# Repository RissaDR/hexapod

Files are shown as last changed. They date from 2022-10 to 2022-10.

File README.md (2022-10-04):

# hexapod

This is a hexapod robot project, designed to be built with 18 HerkuleX DRS-0101 servos. The frame of the hexapod robot was initially intended to be build with acrylic (plexiglass) sheets and hand-cut, but after some attempts at cutting the acrylic, it was decided it would be more efficient and accurate to 3D print the frame instead.

The constructed hexapod with the servos and 3D printed parts:

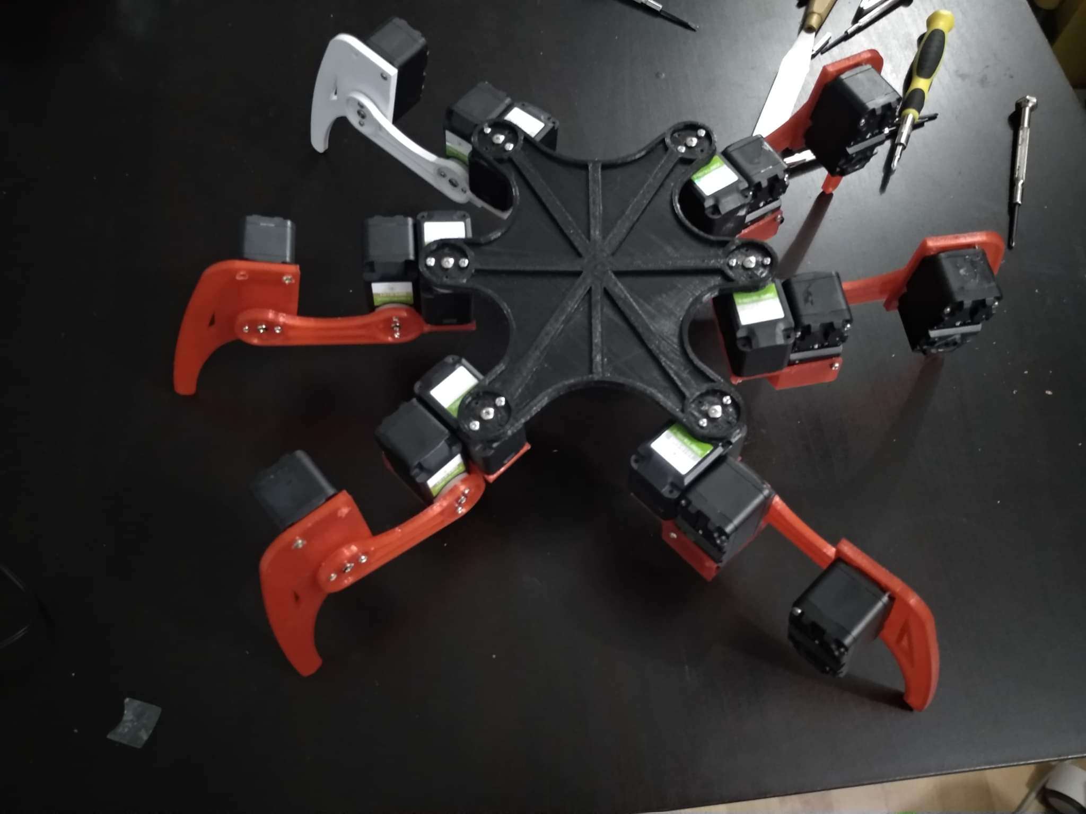
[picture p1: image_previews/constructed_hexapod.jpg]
Constructed hexapod


## Simulation of kinematics

With help from a [hexapod robot simulator](https://github.com/mithi/hexapod) the inverse kinematics of the robot and its corresponding servo movements were solved by scripting a gait simulator with a skeleton hexapod model made in Blender using Python.

Simulating kinematics with a Python script to animate skeleton hexapod model in Blender:

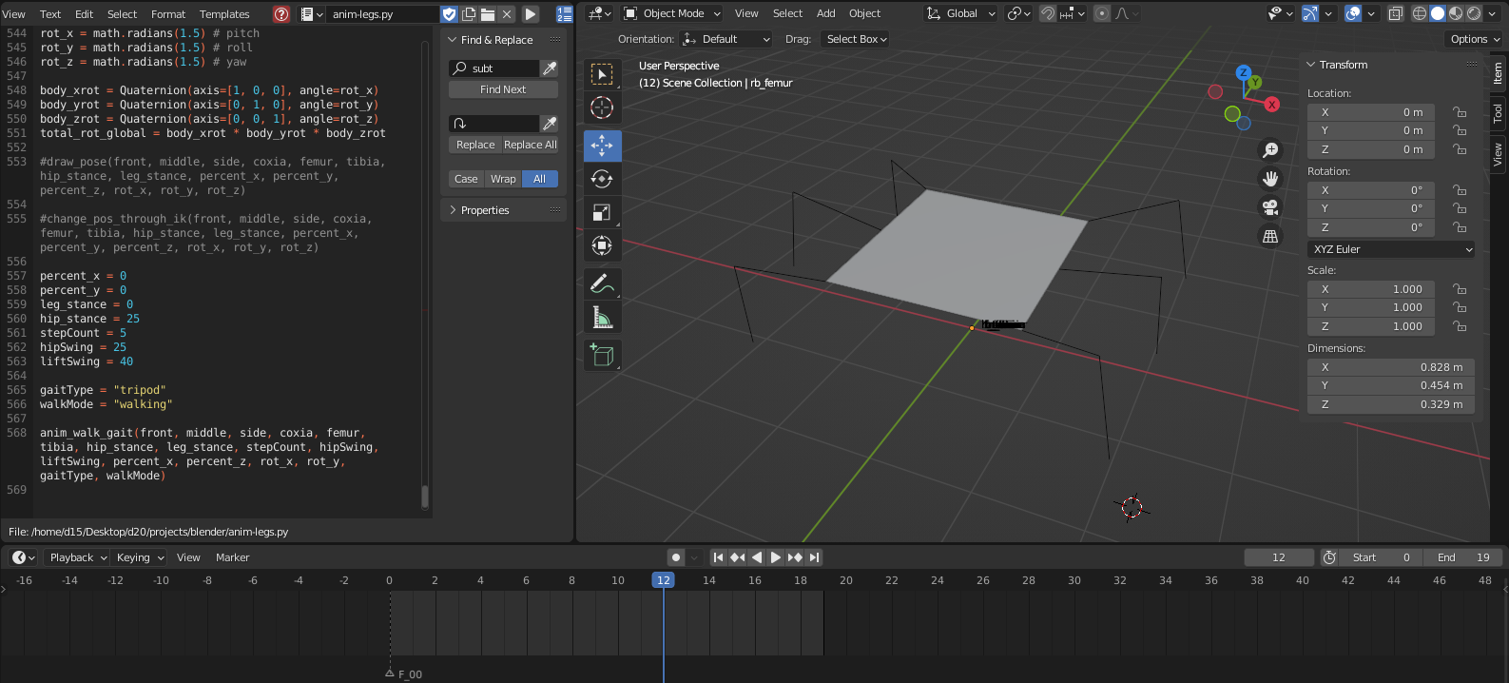
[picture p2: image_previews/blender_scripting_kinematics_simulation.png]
Simulating kinematics with a Python script on a skeleton hexapod model in Blender


## Creation of the hexapod frame

The hexapod frame was modelled with mainly the measurements and the dimensions, as well as movement range of the HerkuleX DRS-0101 servos in mind. Before switching over to 3D printed this model was used to create the acrylic blueprints to cut out the hexapod frame. The frame was modelled to size using Blender in `model/blender/my_hexapod_frame.blend` and exported to .stl and then used Cura to generate its .gcode to print with a 3D printer using Pronterface. 

Through several printing trials the scale of some of the parts of the frame were slightly adjusted and the .stl and .gcode of iterations of these trials are in the repository in `model/blender/stl/` and `model/blender/gcode/` respectively.

3D model of hexapod in Blender, with parts positioned as they would be constructed:

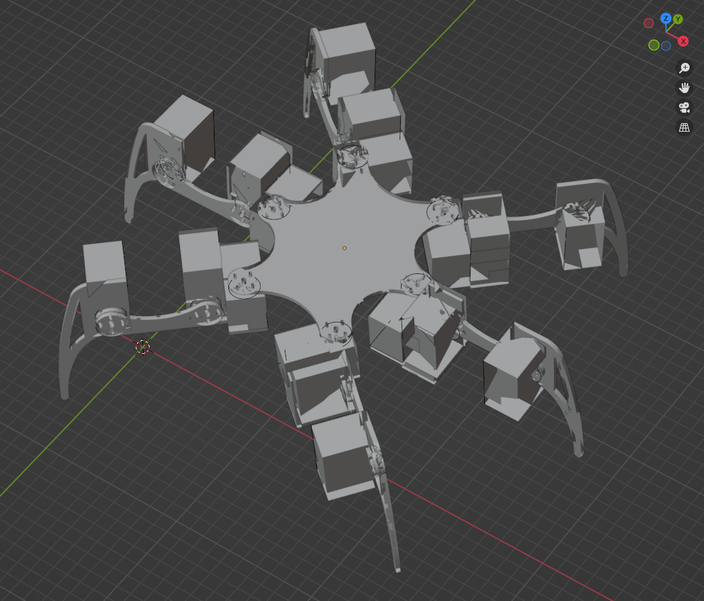
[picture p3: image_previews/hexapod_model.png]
3D model of hexapod in Blender


Wireframe of 3D model:

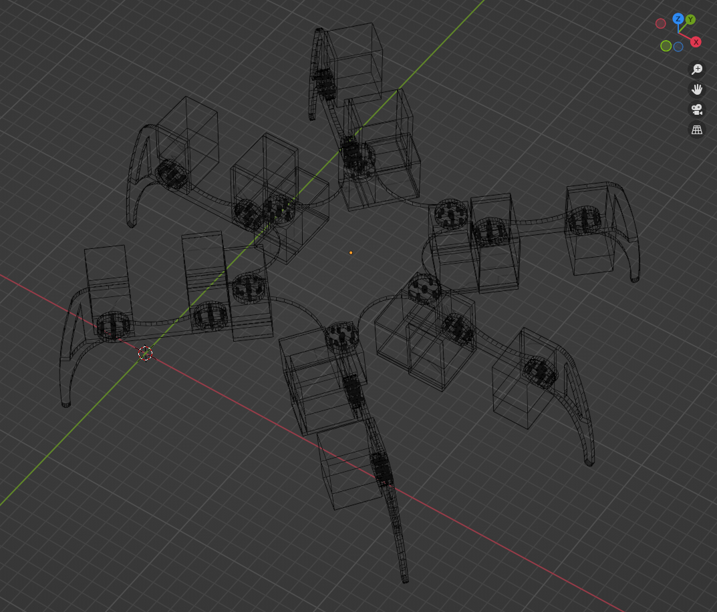
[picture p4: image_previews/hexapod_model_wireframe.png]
3D model of hexapod in Blender, wireframe view


Overview of parts on acrylic blueprint from `model/acrylic_blueprints/`:

Overview of parts on acrylic blueprint

## Interfacing with the servos

To interface with and move the servos an Arduino microcontroller was used; with an ESP32 microcontroller the servos on the hexapod could also be controlled using Wi-Fi/Bluetooth. To test for driver issues on the motor this project also wrote some test scripts in Python.

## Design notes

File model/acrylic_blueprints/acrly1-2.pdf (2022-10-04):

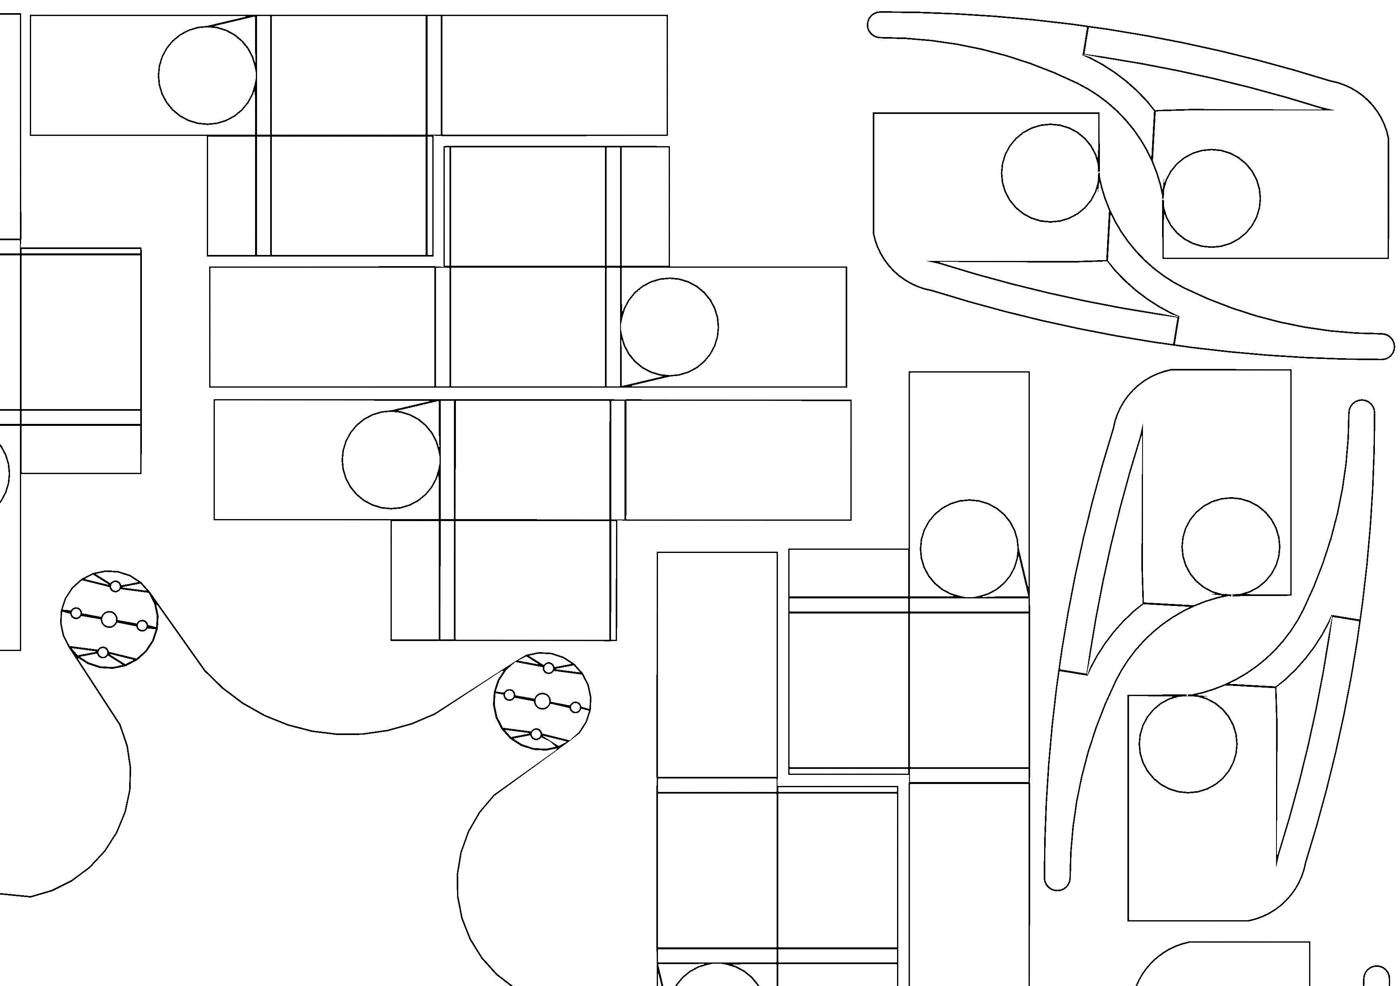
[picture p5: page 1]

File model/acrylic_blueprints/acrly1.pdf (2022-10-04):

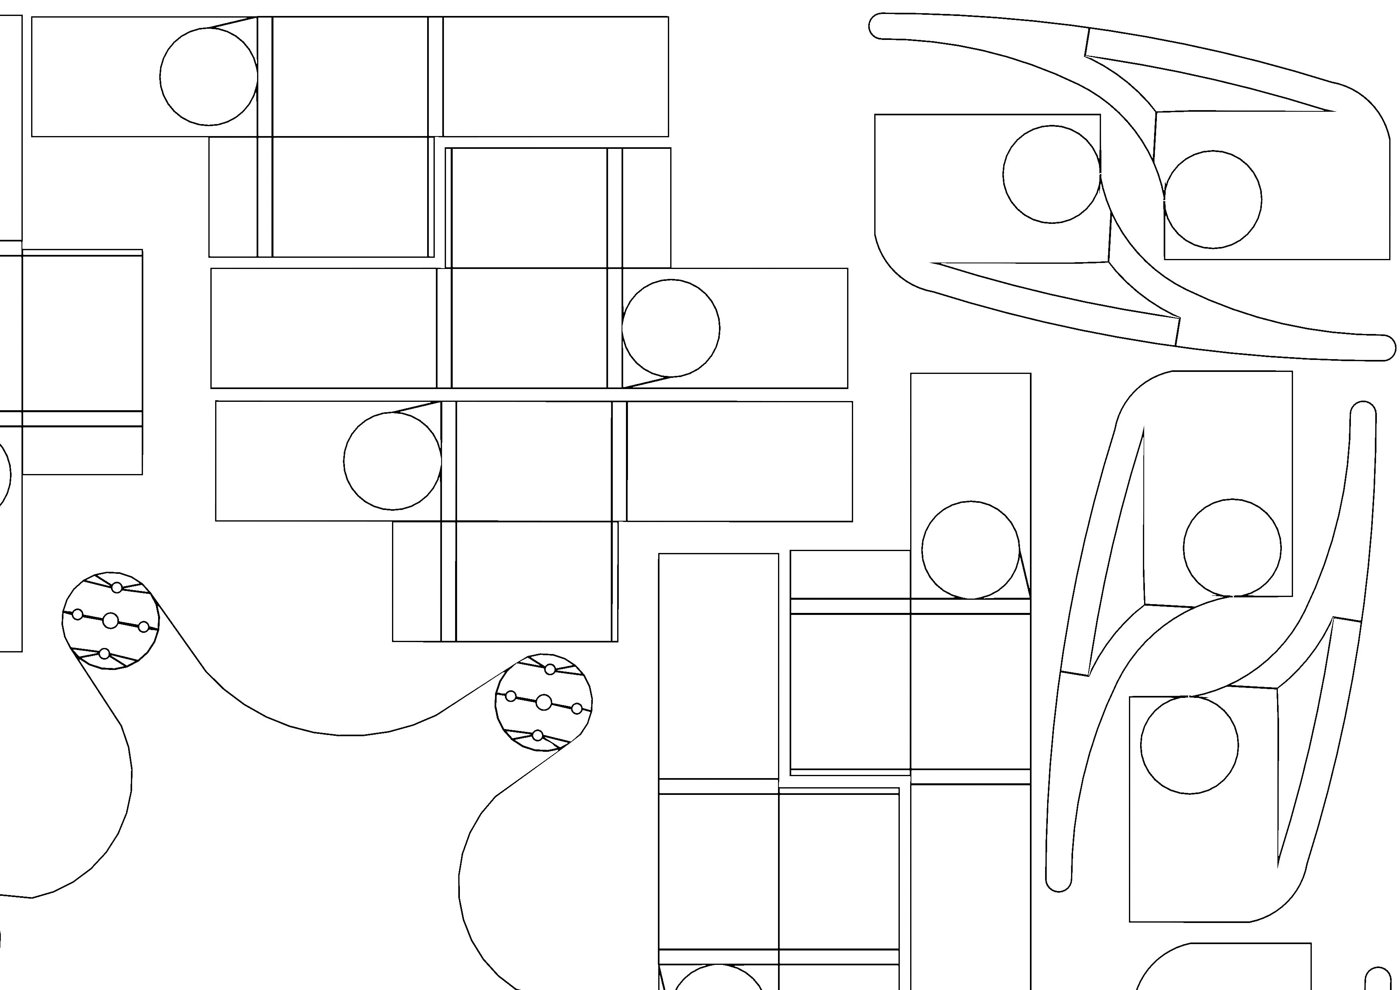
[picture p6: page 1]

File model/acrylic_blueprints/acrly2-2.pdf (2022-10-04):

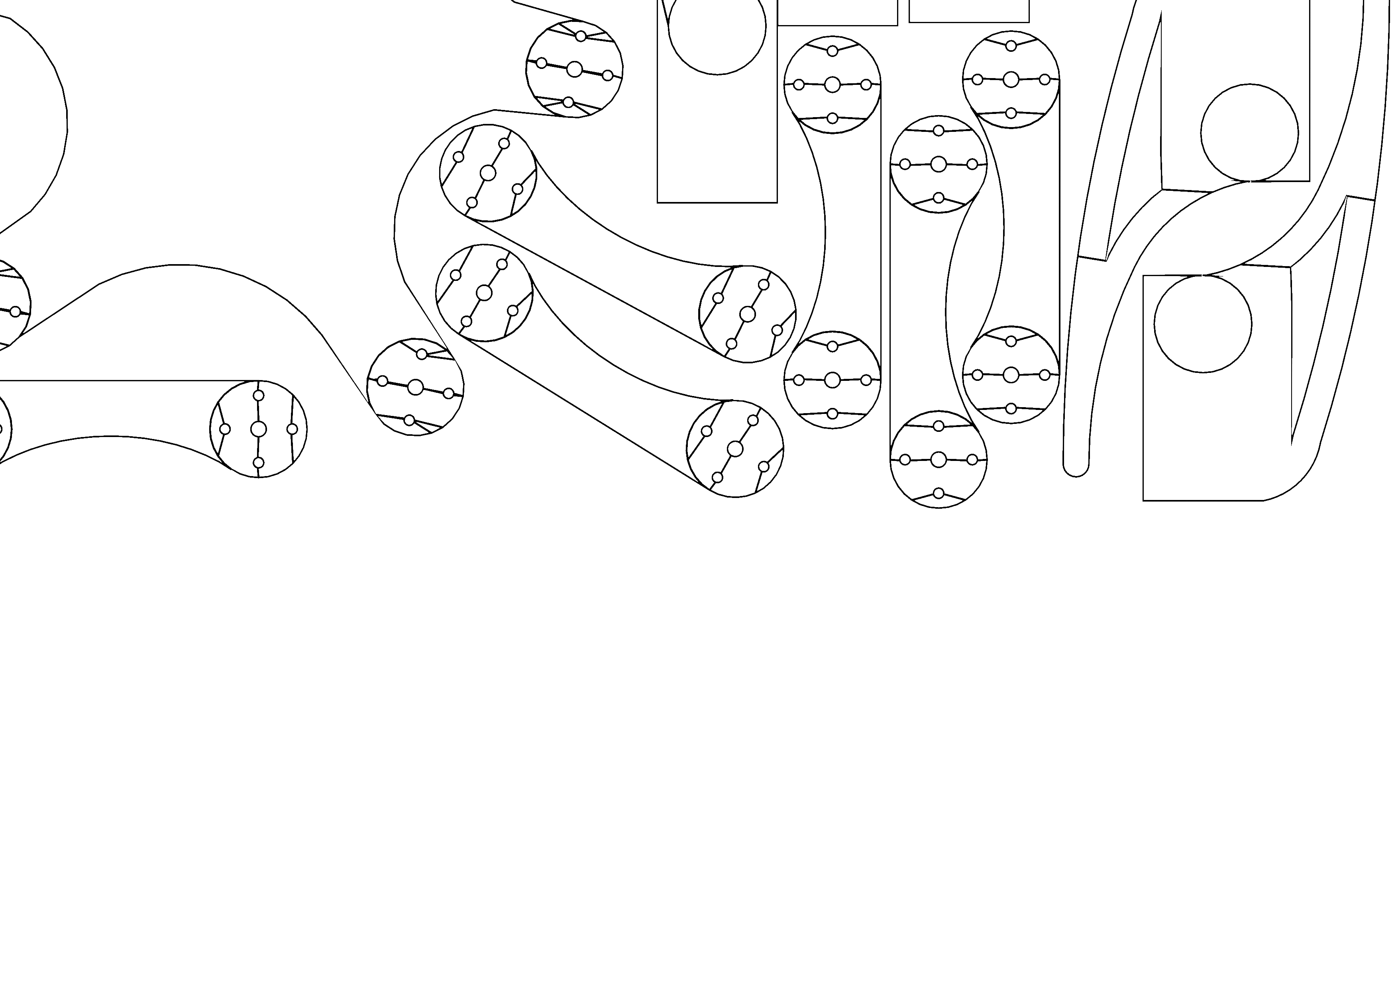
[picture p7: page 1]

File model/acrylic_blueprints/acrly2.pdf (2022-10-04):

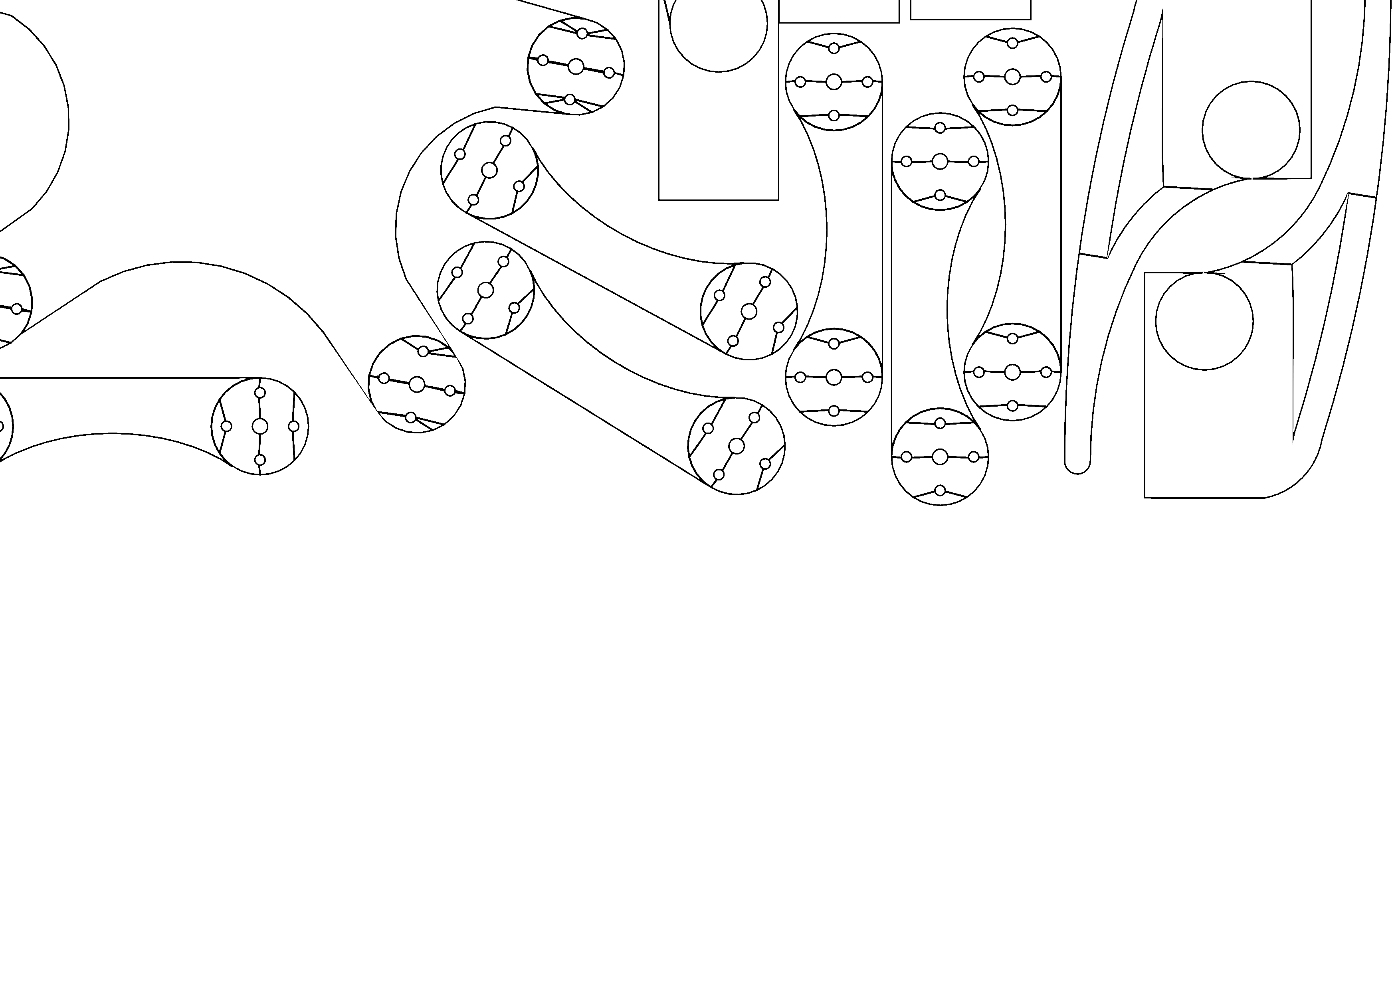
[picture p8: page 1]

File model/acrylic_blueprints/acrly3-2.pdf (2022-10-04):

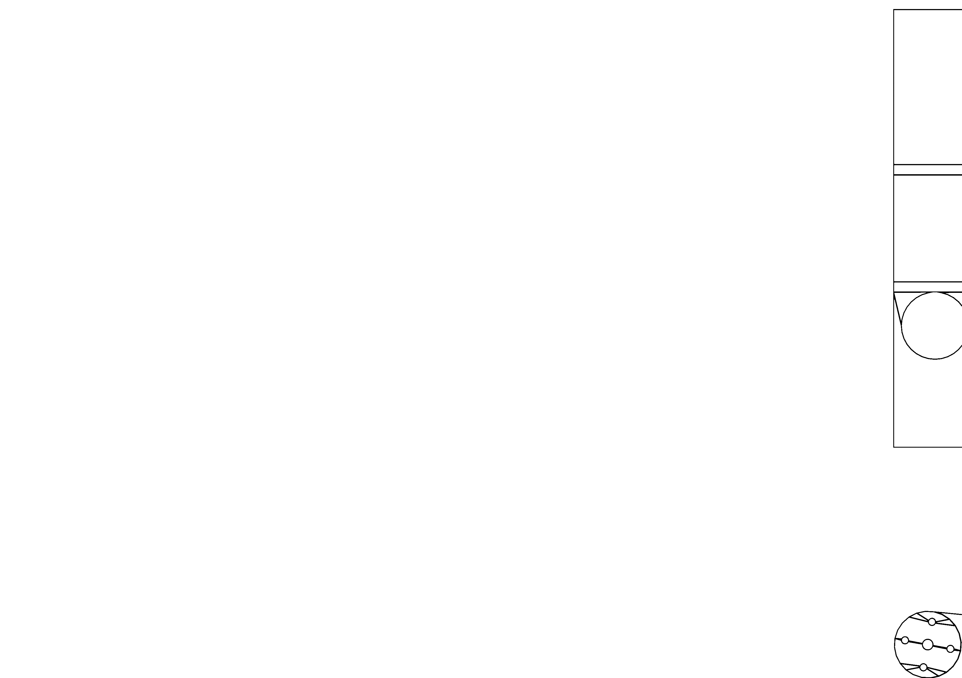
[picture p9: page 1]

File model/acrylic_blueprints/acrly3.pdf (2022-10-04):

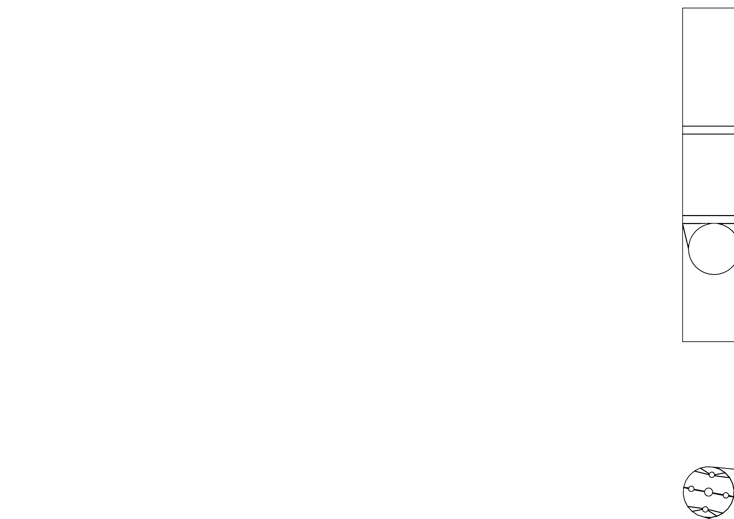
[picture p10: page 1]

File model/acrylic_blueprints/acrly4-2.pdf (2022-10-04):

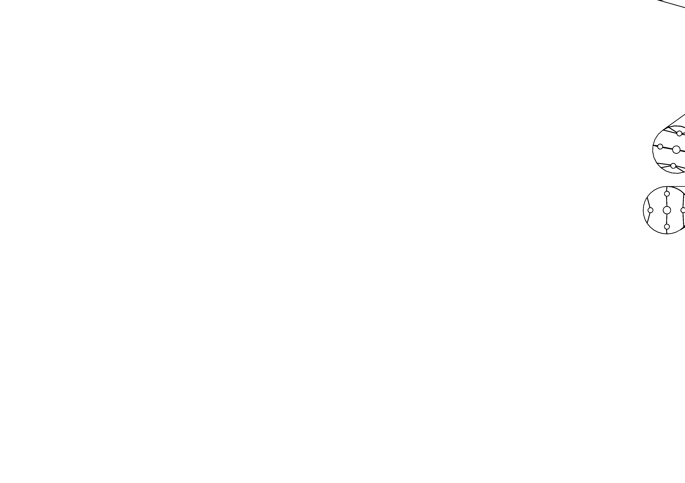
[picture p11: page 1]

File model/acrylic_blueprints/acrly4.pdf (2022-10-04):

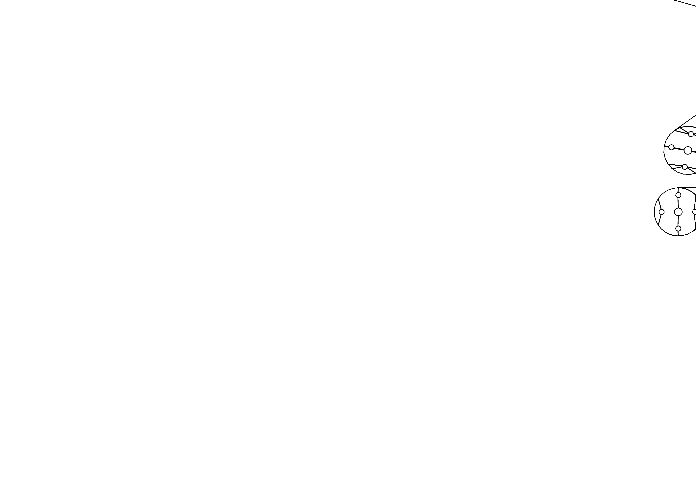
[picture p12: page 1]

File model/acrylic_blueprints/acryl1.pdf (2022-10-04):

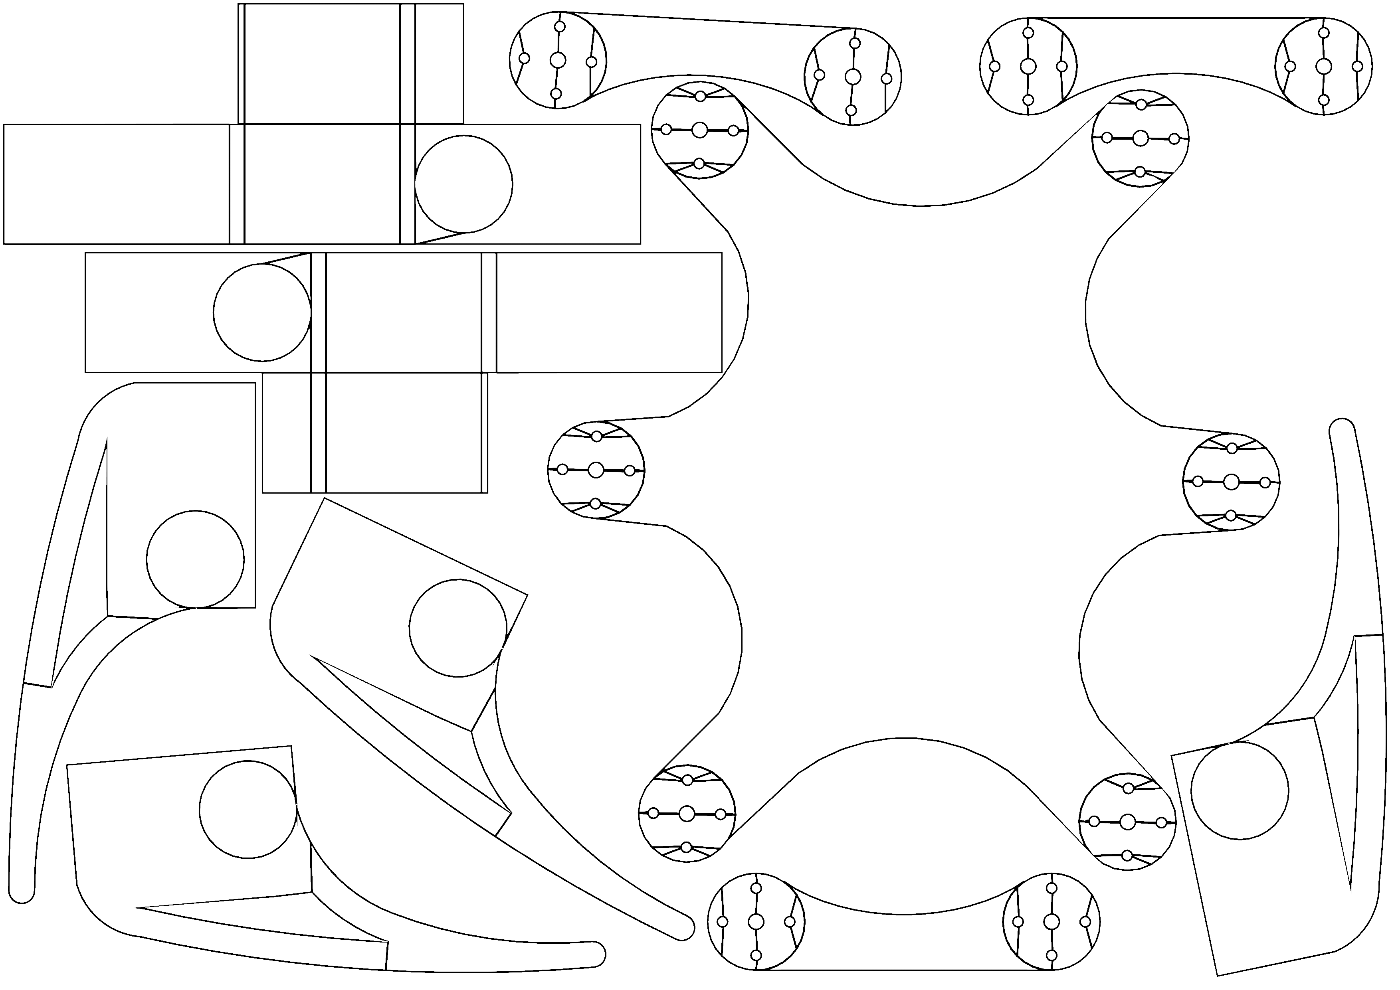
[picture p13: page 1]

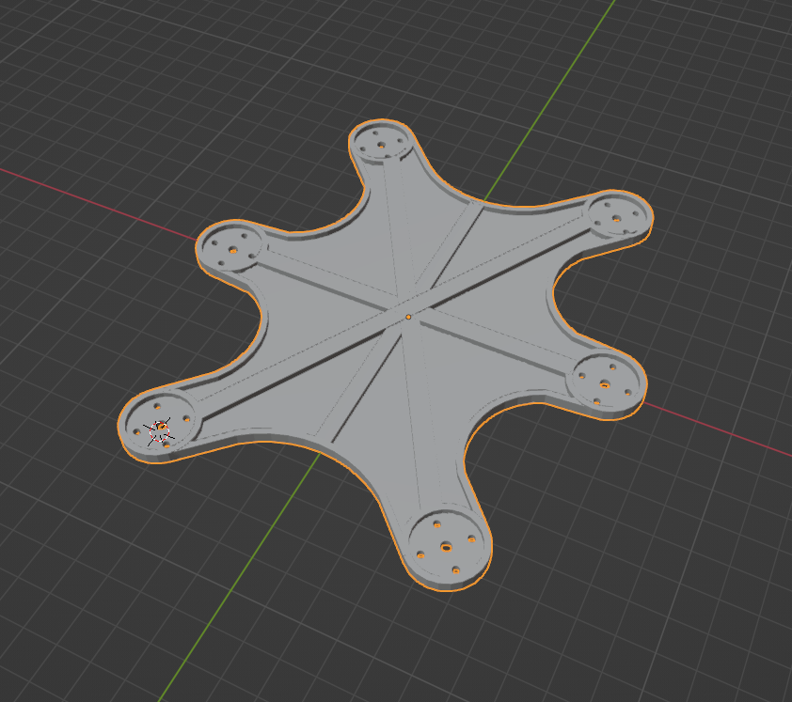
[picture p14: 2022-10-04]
image_previews/3d_model.png

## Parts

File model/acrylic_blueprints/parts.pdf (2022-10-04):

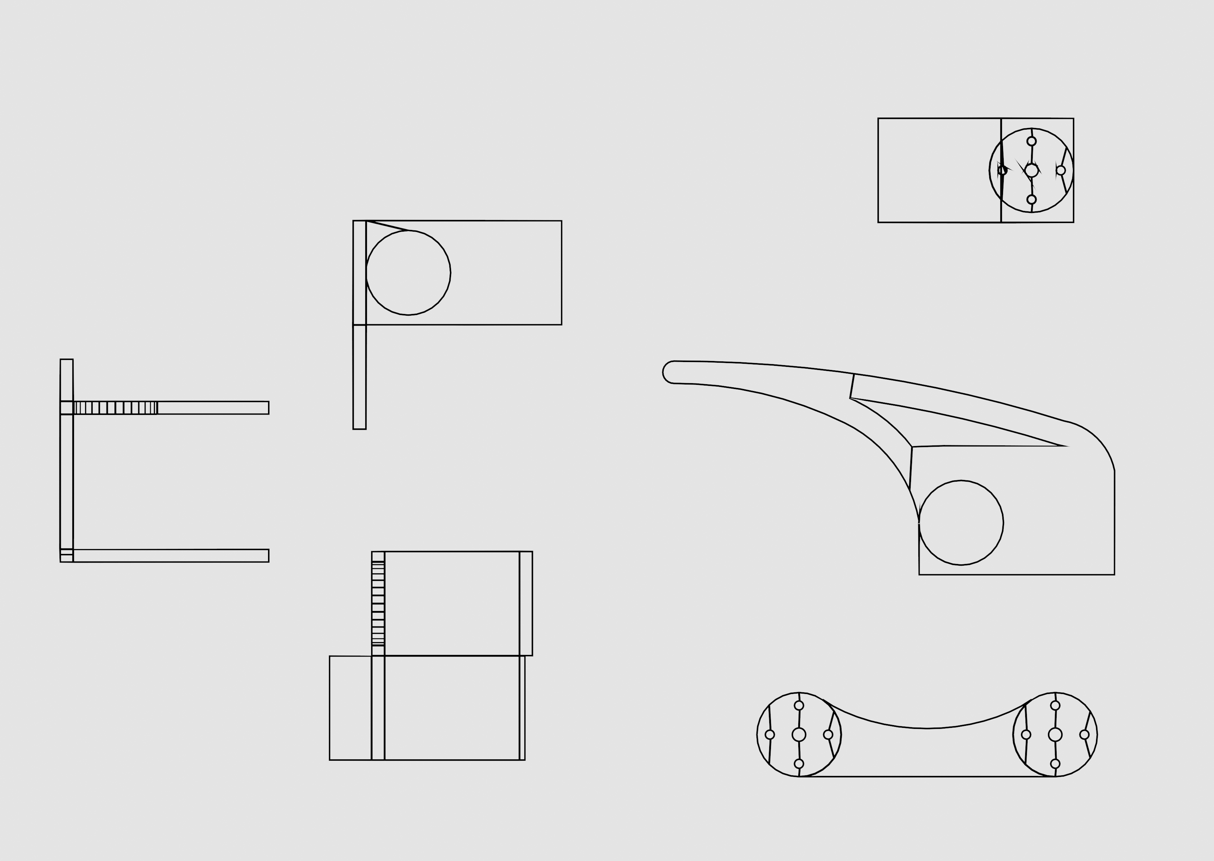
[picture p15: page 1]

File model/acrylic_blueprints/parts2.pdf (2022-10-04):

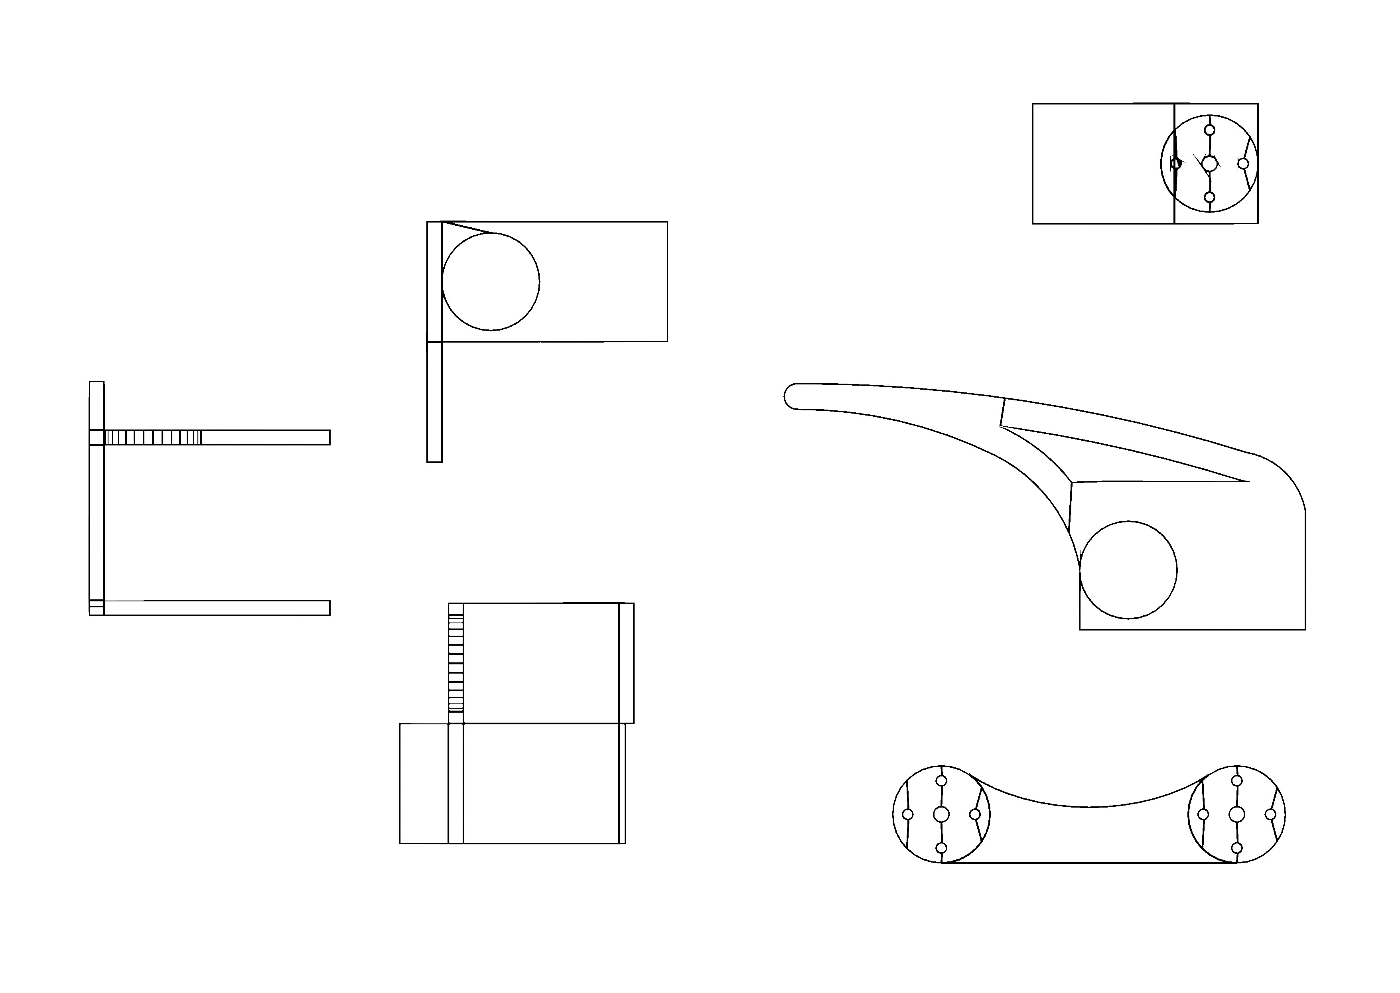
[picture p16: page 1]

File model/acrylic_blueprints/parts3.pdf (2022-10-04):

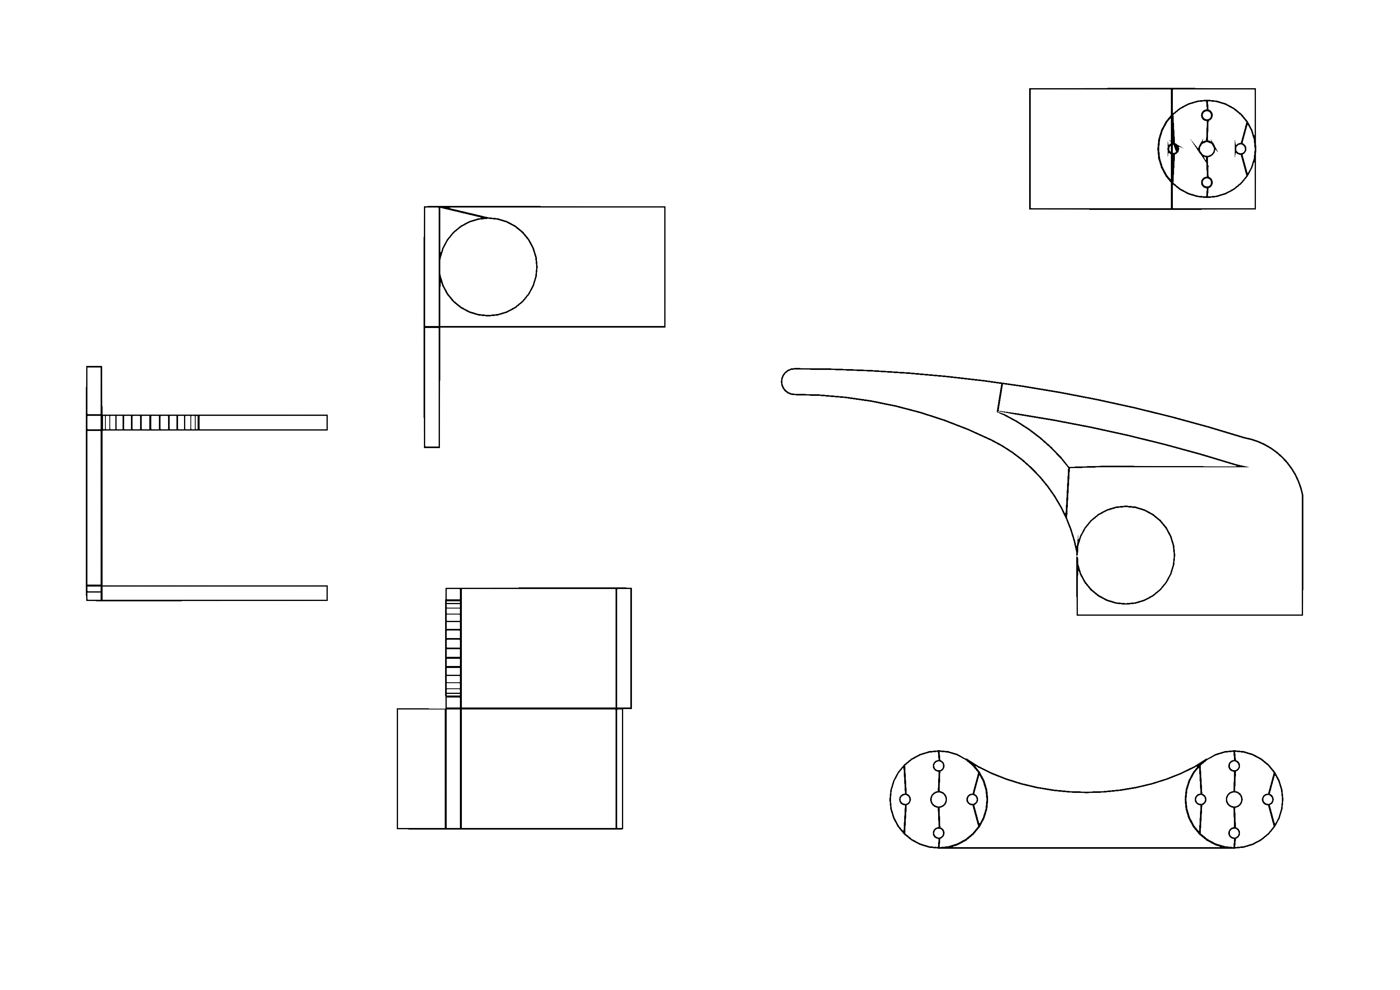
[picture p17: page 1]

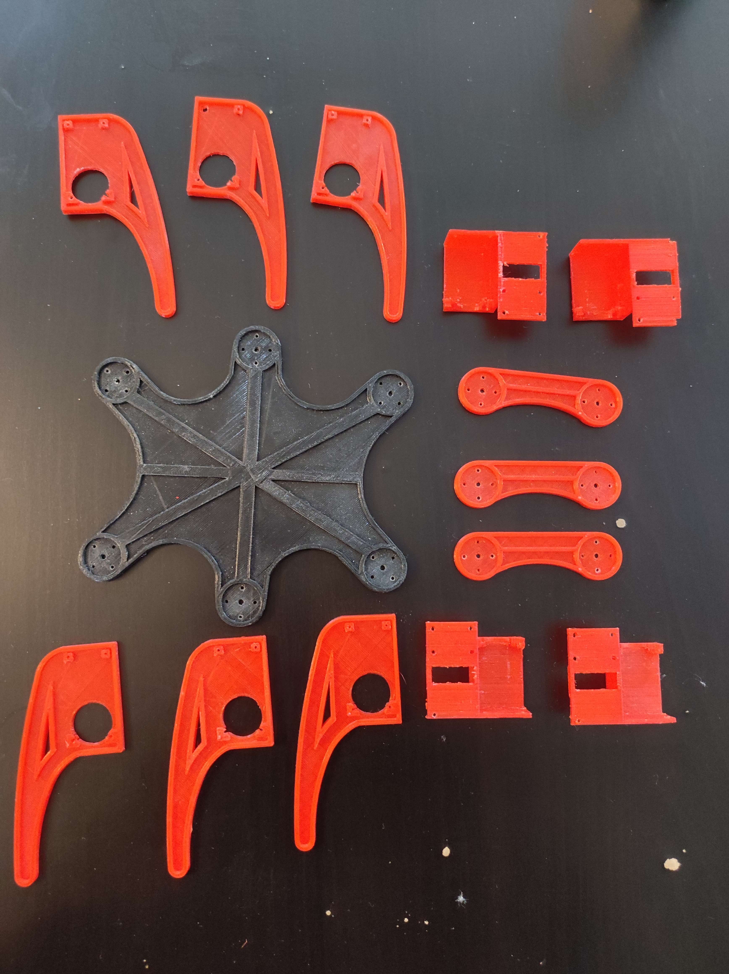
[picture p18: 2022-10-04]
image_previews/parts_preview.jpg

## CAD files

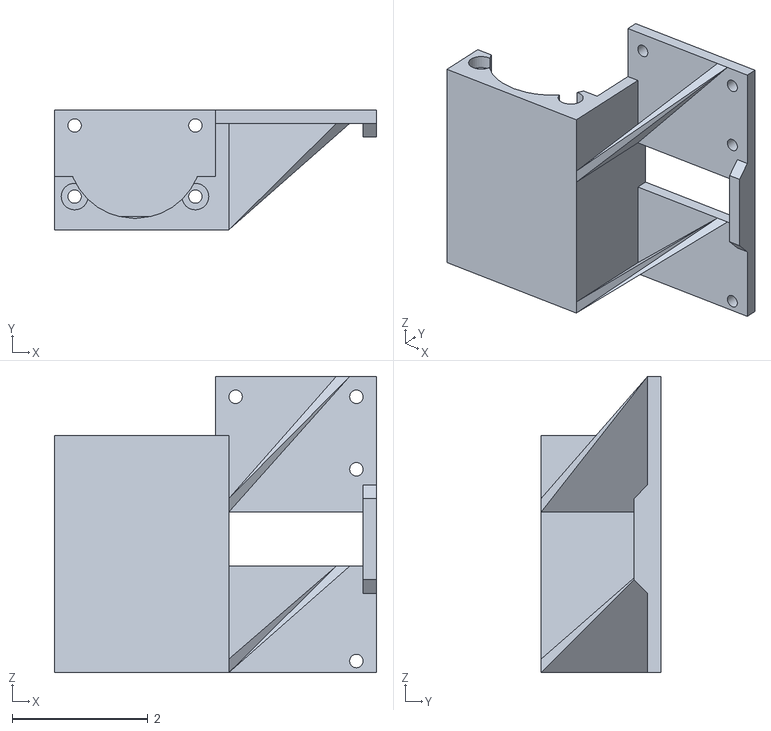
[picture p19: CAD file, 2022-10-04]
model/stl/final/_CF.stl
4.75 x 1.76 x 4.37

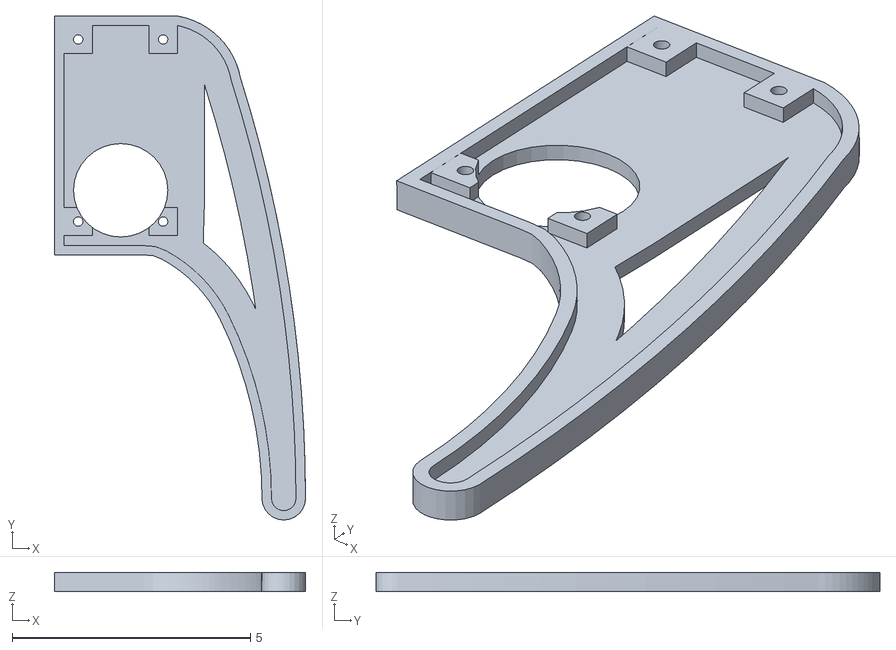
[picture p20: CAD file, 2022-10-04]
model/stl/versioned/_TIBIAx9998_w_SCL2_WALL.stl
5.27 x 10.6 x 0.4

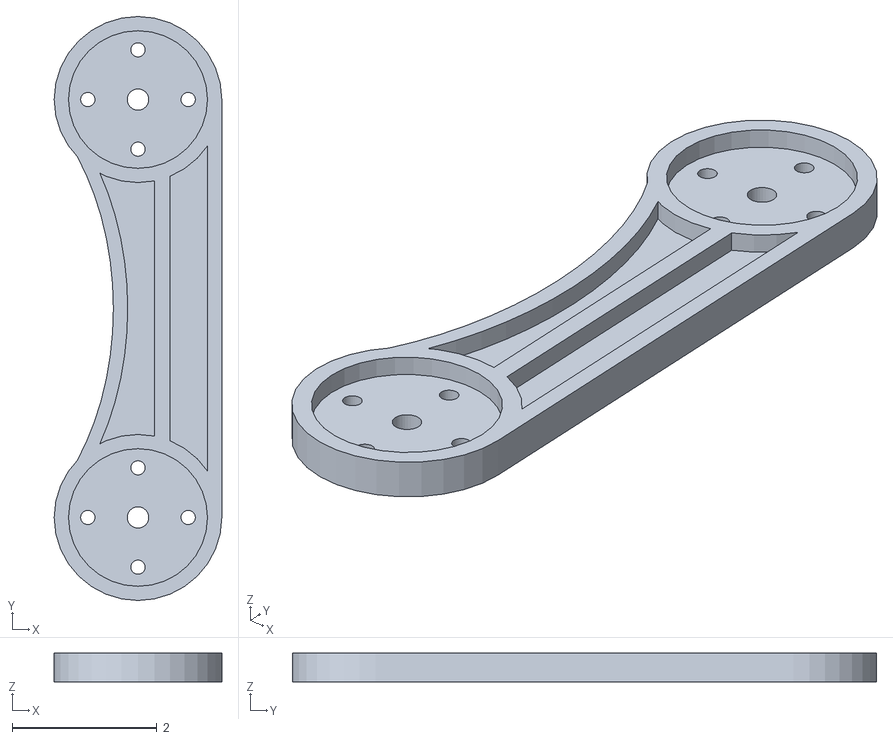
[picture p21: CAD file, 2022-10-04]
model/stl/final/_FEMUR.stl
2.32 x 8.07 x 0.4

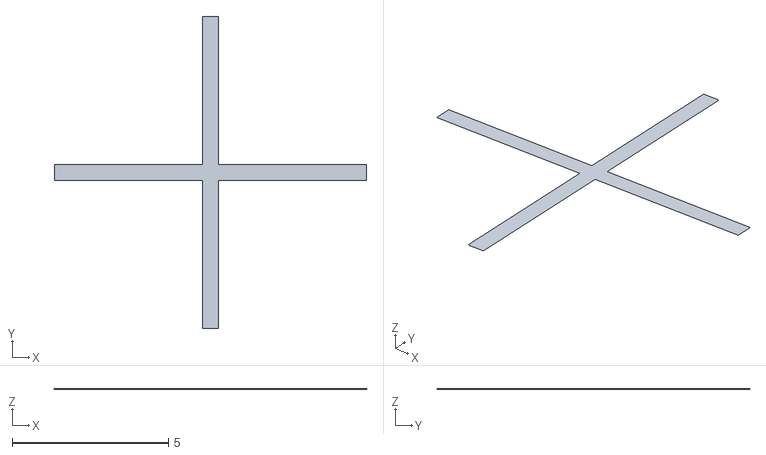
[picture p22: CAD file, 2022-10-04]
model/stl/versioned/kyds2.stl
10.0 x 10.0 x 0.01

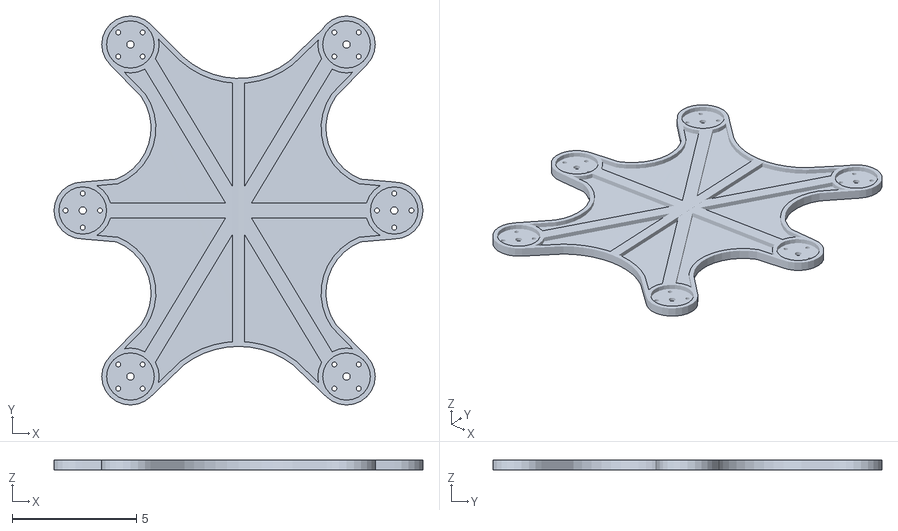
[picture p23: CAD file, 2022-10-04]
model/stl/final/_BASE.stl
14.9 x 15.7 x 0.404

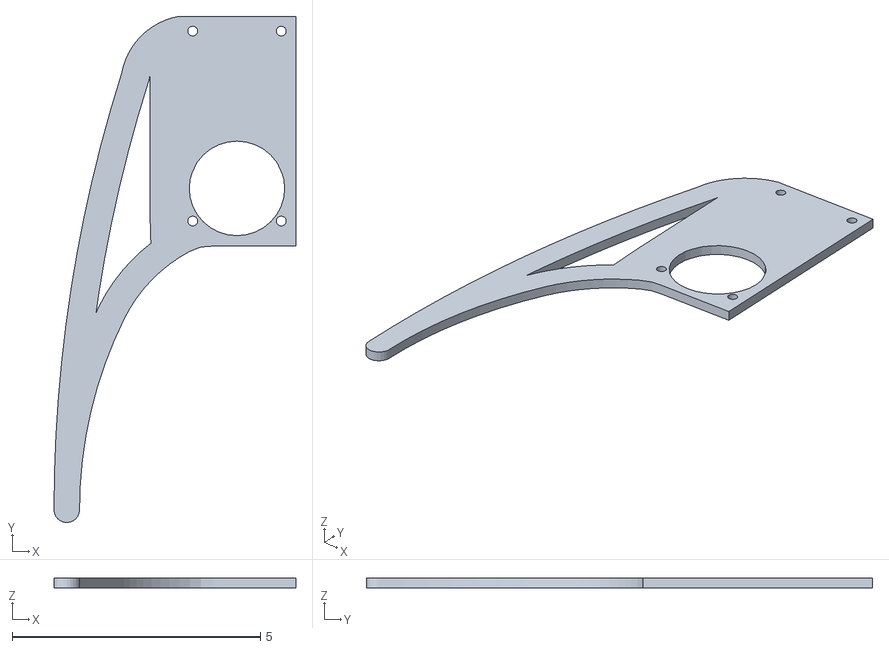
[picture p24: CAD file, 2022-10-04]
model/stl/versioned/_TIBIAx99986.stl
4.87 x 10.2 x 0.2

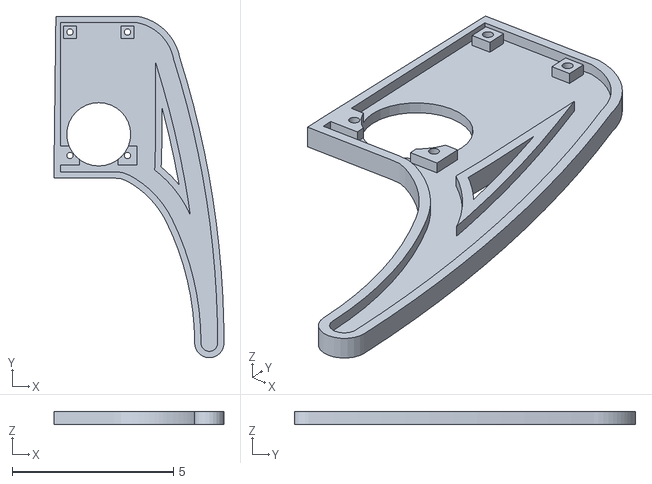
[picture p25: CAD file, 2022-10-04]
model/stl/final/_TIBIA.stl
5.27 x 10.6 x 0.4

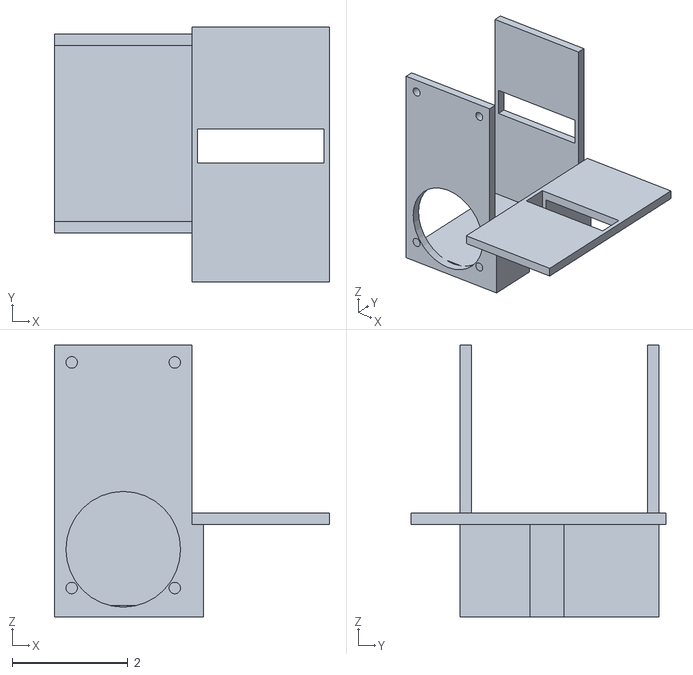
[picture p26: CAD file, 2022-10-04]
model/stl/versioned/_COXIA_FEMUR_FRAMEx9998.stl
4.75 x 4.41 x 4.70

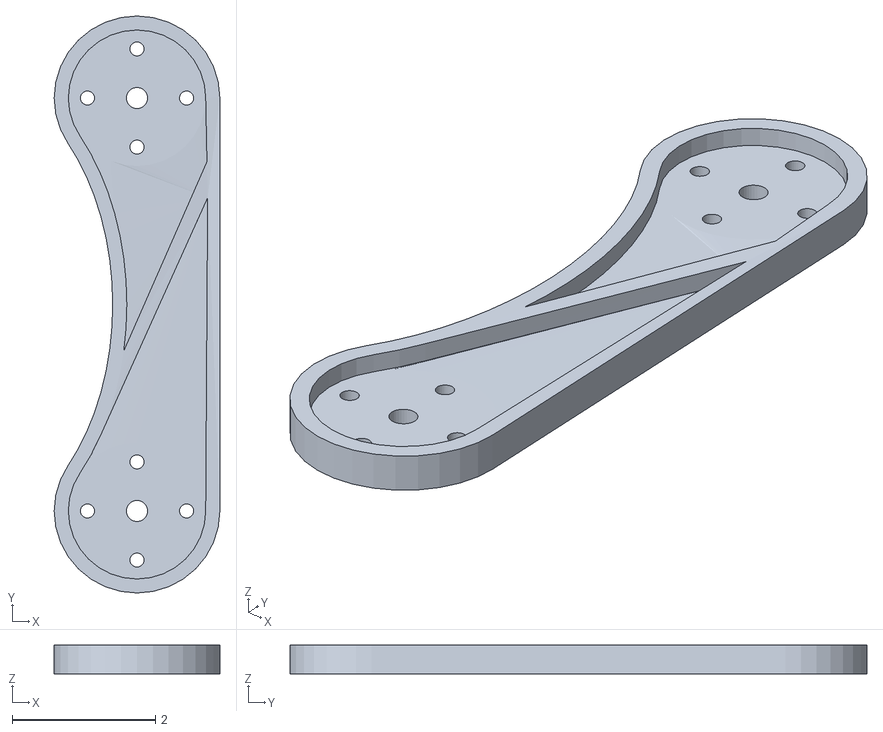
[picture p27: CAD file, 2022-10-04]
model/stl/versioned/_FEMUR_WALL_4cm2cmLINE2.stl
2.32 x 8.07 x 0.4

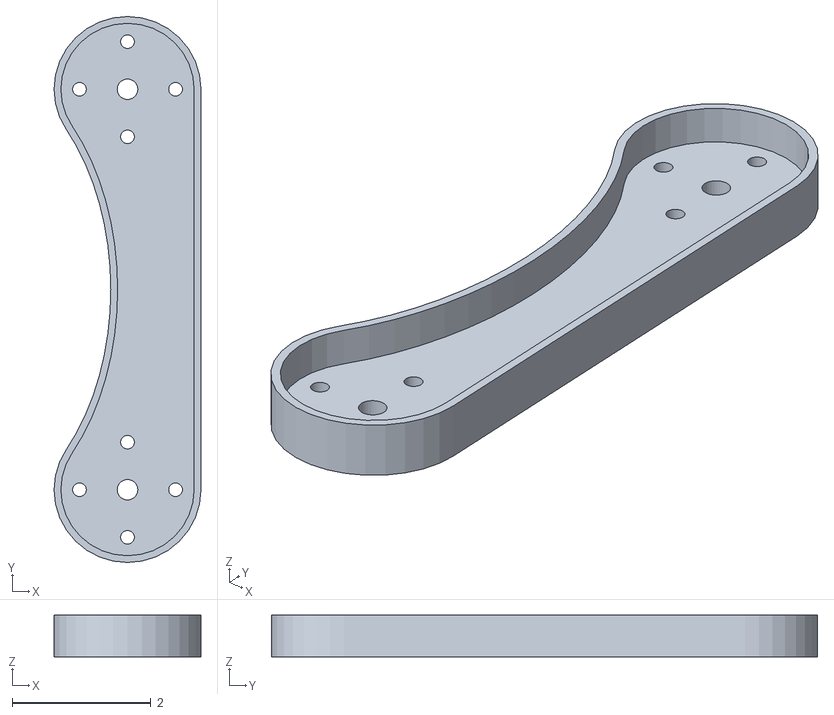
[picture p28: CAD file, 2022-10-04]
model/stl/versioned/_FEMUR_WALL_6cm1cm.stl
2.12 x 7.87 x 0.6

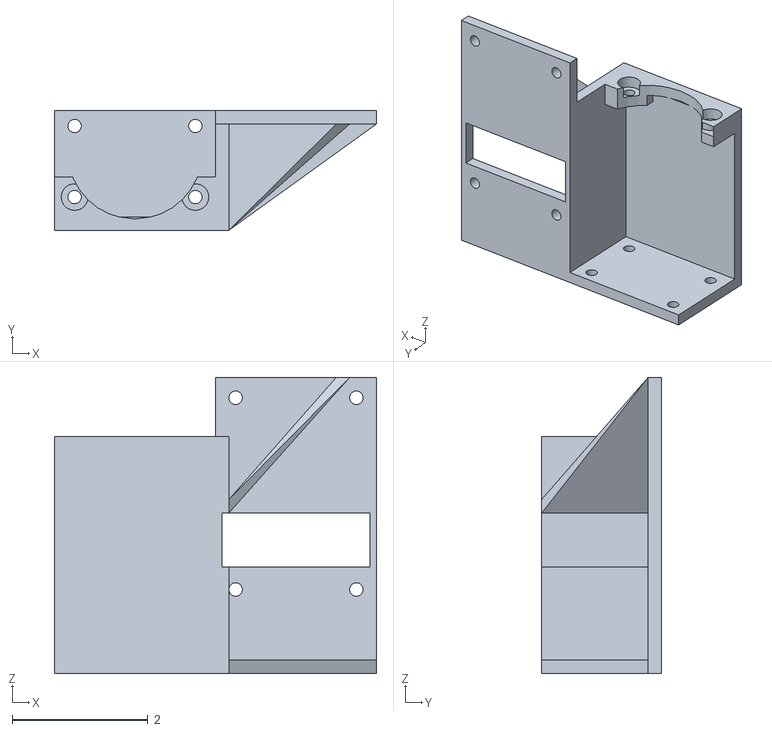
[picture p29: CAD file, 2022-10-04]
model/stl/versioned/_FC2x98996.stl
4.75 x 1.76 x 4.37

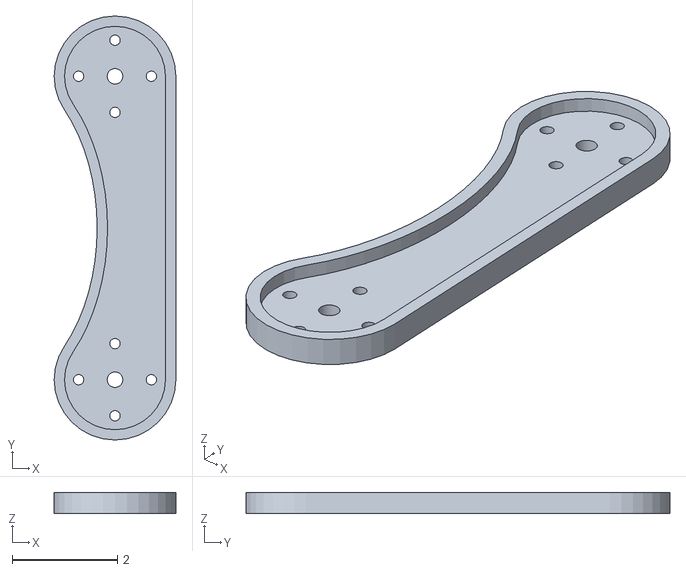
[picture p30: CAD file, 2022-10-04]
model/stl/versioned/_FEMUR_WALL_4cm2cm.stl
2.32 x 8.07 x 0.4

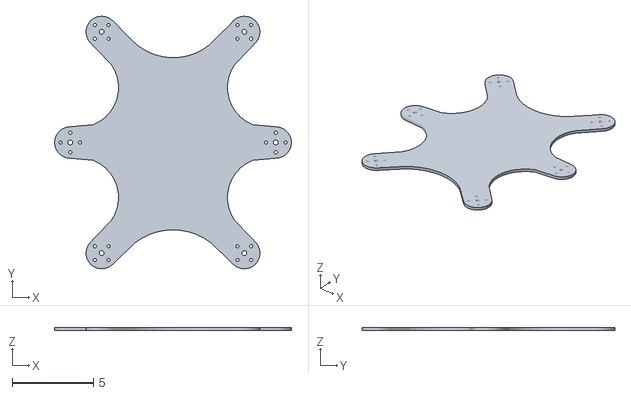
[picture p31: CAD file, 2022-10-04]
model/stl/versioned/_BODYx100.stl
14.6 x 15.6 x 0.2

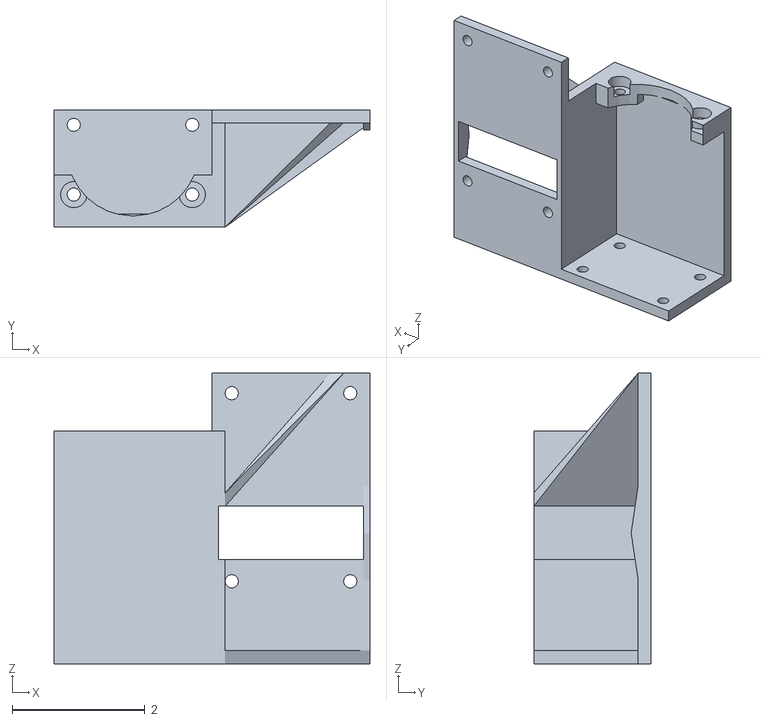
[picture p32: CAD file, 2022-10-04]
model/stl/versioned/_FC2x989989.stl
4.75 x 1.76 x 4.37

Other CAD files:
model/stl/versioned/_FC2x98994.stl
model/stl/versioned/_COXIA_FEMUR_FRAMEx99982.stl
model/stl/versioned/_TIBIAx99985.stl
model/stl/versioned/_SERVO_BASEvX_CIRCLE_TEST.stl
kinematics/blender/scripting.blend
model/stl/versioned/_BASE.stl
model/stl/versioned/_CF01.stl
model/stl/versioned/_COXIA_FEMUR_FRAMEx100.stl
model/stl/versioned/_FC2x9899.stl
model/stl/versioned/_FC2x98992.stl
model/stl/versioned/_FC2x98993.stl
model/stl/versioned/_FC2x98995TEST.stl
model/stl/versioned/_FC2x98995TEST2.stl
model/stl/versioned/_FC2x98997.stl
model/stl/versioned/_FC2x98998.stl
model/stl/versioned/_FC2x989988.stl
model/stl/versioned/_FCx9899.stl
model/stl/versioned/_FEMUR2.stl
model/stl/versioned/_FEMUR4cm.stl
model/stl/versioned/_FEMUR_WALL_4cm2cmLINE.stl
model/stl/versioned/_FEMUR_WALL_6cm.stl
model/stl/versioned/_FEMURx100.stl
model/stl/versioned/_HoleTest.stl
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

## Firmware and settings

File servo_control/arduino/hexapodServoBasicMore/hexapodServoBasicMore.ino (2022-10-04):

#define NUM_OF_SERVOS 18

uint8_t servos[NUM_OF_SERVOS] = {1, 2, 3, 4, 5, 6, 7, 8, 9, 10, 11, 12, 13, 14, 15, 16, 17, 18};
uint16_t pose1[NUM_OF_SERVOS] = {250, 250, 250, 250, 250, 250, 250, 250, 250, 250, 250, 250, 250, 250, 250, 250, 250, 250};
uint16_t pose2[NUM_OF_SERVOS] = {750, 750, 750, 750, 750, 750, 750, 750, 750, 750, 750, 750, 750, 750, 750, 750, 750, 750};

uint8_t leg1[3] = {0, 1, 2};
uint8_t leg2[3] = {3, 4, 5};
uint8_t leg3[3] = {6, 7, 8};
uint8_t leg4[3] = {9, 10, 11};
uint8_t leg5[3] = {12, 13, 14};
uint8_t leg6[3] = {15, 16, 17};

uint8_t *legs[6] = {leg1, leg2, leg3, leg4, leg5, leg6};

void setup() {
  Serial.begin(115200);
  clearError();
  disableACK();
  torqueOn();
  
//  pose1[leg1[0]] = 0;
//  pose1[leg1[1]] = 0;
//  pose1[leg1[2]] = 0;
//  
//  pose2[leg1[0]] = 100;
//  pose2[leg1[1]] = 100;
//  pose2[leg1[2]] = 100;
  
  //pose1[*legs[1][0]
  
//  pose1[3] = 200;
//  pose1[leg2[0]] = 400;
//  pose1[legs[1][0]] = 100;
//  pose1[legs[1][1]] = 120;
//  pose1[legs[1][2]] = 150;
  setLeg(pose1, 0, 0, 0, 0);
  setLeg(pose1, 1, 0, 0, 0);
  
//  pose2[legs[1][0]] = 700;
  setLeg(pose2, 0, 100, 100, 100);
  setLeg(pose2, 1, 100, 100, 100);
  
  
}

void loop() {
  targetPosition(NUM_OF_SERVOS, servos, pose1, 1);
  delay(1000);
  targetPosition(NUM_OF_SERVOS, servos, pose2, 2);
  delay(1000);

}

void setLeg(uint16_t *pose, uint8_t leg, uint16_t pos1, uint16_t pos2, uint16_t pos3) {
  pose[legs[leg][0]] = pos1;
  pose[legs[leg][1]] = pos2;
  pose[legs[leg][2]] = pos3;
}

void targetPosition(uint8_t len, uint8_t *servoIds, uint16_t *pos, uint8_t color) {
  for (int i = 0; i < len; i++) {
    moveServo(servoIds[i], pos[i], color);
  }
}

void torqueOn() {
  uint8_t data[10];
  data[0] = 0xFF; // header 1
  data[1] = 0xFF; // header 2
  data[2] = 10; // length
  data[3] = 0xFE; // servo id
  data[4] = 0x03; // CMD id

  data[7] = 0x34; // register
  data[8] = 0x01; // length
  data[9] = 0x60; // value 

  data[5] = (data[2] ^ data[3] ^ data[4] ^ data[7] ^ data[8] ^ data[9]) & 0xFE; // checksum1
  data[6] = (~data[5]) & 0xFE; // checksum2

  for (int i = 0; i < 10; i++) {
    Serial.write(data[i]);
  }
  
}

void moveServo(uint8_t servoId, uint16_t pos, uint8_t color) {
  
  uint8_t lo_pos;
  uint8_t hi_pos;
  lo_pos = (uint8_t) pos;
  hi_pos = (uint8_t) (pos >> 8);
  
  uint8_t data[12];
  data[0] = 0xFF; // header 1
  data[1] = 0xFF; // header 2
  data[2] = 12; // length
  data[3] = servoId; // servo id
  data[4] = 0x06; // CMD id

  data[7] = 60; // playtime
  data[8] = lo_pos; // jog lsb
  data[9] = hi_pos; // jog msb
  //color = color & 0x03;
  data[10] = color;//(color << 2) & (~0x02); // set
  data[11] = servoId; // id

  data[5] = (data[2] ^ data[3] ^ data[4] ^ data[7] ^ data[8] ^ data[9] ^ data[10] ^ data[11]) & 0xFE; // checksum1
  data[6] = (~data[5]) & 0xFE; // checksum2

  for (int i = 0; i < 12; i++) {
    Serial.write(data[i]);
  }

}

void disableACK() {
  uint8_t data[10];
  data[0] = 0xFF; // header 1
  data[1] = 0xFF; // header 2
  data[2] = sizeof(data)/sizeof(data[0]); // length
  data[3] = 0xFE; // servo id
  data[4] = 0x03; // CMD id

  data[7] = 1; // register
  data[8] = 0x01; // length
  data[9] = 1; // value 

  data[5] = (data[2] ^ data[3] ^ data[4] ^ data[7] ^ data[8] ^ data[9]) & 0xFE;
  data[6] = (~data[5]) & 0xFE;

//  Serial.println("Hello world");
//  return;
  for (int i = 0; i < 10; i++) {
    Serial.write(data[i]);
  }
  
}

void clearError() {
  uint8_t data[11];
  data[0] = 0xFF; // header 1
  data[1] = 0xFF; // header 2
  data[2] = 11; // length
  data[3] = 0xFE; // servo id
  data[4] = 0x03; // CMD id

  data[7] = 0x30; // register
  data[8] = 0x02; // length
  data[9] = 0x00; // value 
  data[10] = 0x00; // value 

  data[5] = (data[2] ^ data[3] ^ data[4] ^ data[7] ^ data[8] ^ data[9] ^ data[10]) & 0xFE;
  data[6] = (~data[5]) & 0xFE;

//  Serial.println("Hello world");
//  return;
  for (int i = 0; i < 11; i++) {
    Serial.write(data[i]);
  }
  
  delay(10);
}

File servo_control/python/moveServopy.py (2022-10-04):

import serial
from time import sleep
import numpy as np

# will later implement a code to find and connect to serial ports

ser = serial.Serial('/dev/ttyUSB0', 115200) # '/dev/ttyUSB0' on linux

def torqueOn():
  data = [0] * 10
  data[0] = 0xFF # header 1
  data[1] = 0xFF # header 2
  data[2] = 10 # length
  data[3] = 0xFE # servo id
  data[4] = 0x03 # CMD id

  data[7] = 0x34 # register
  data[8] = 0x01 # length
  data[9] = 0x60 # value 

  data[5] = (data[2] ^ data[3] ^ data[4] ^ data[7] ^ data[8] ^ data[9]) & 0xFE # checksum1
  data[6] = (~data[5]) & 0xFE # checksum2

  i = 0
  while(i < 10):
    #print(data[i])
    ser.write(bytes([data[i]]))
    i += 1

def turnLED(sid, colour):
  data = [0] * 10
  data[0] = 0xFF # header 1
  data[1] = 0xFF # header 2
  data[2] = 10 # length
  data[3] = sid # servo id
  data[4] = 0x03 # CMD id

  data[7] = 0x35 # register
  data[8] = 0x01 # length
  data[9] = colour # value 

  data[5] = (data[2] ^ data[3] ^ data[4] ^ data[7] ^ data[8] ^ data[9]) & 0xFE
  #print("checksum1: ", hex(data[5]))
  data[6] = (~data[5]) & 0xFE
  #print("checksum2: ", hex(data[6]))

  i = 0
  while(i < 10):
    #print(data[i])
    ser.write(bytes([data[i]]))
    i += 1

def changeIDRAM(sid, newid):
  data = [0] * 10
  data[0] = 0xFF # header 1
  data[1] = 0xFF # header 2
  data[2] = 10 # length
  data[3] = sid # servo id
  data[4] = 0x03 # CMD id

  data[7] = 0x00 # register
  data[8] = 0x01 # length
  data[9] = newid # value 

  data[5] = (data[2] ^ data[3] ^ data[4] ^ data[7] ^ data[8] ^ data[9]) & 0xFE
  #print("checksum1: ", hex(data[5]))
  data[6] = (~data[5]) & 0xFE
  #print("checksum2: ", hex(data[6]))

  i = 0
  while(i < 10):
    #print(i, data[i])
    ser.write(bytes([data[i]]))
    i += 1

def clearError():
  data = [0] * 11
  data[0] = 0xFF # header 1
  data[1] = 0xFF # header 2
  data[2] = 11 # length
  data[3] = 0xFE # servo id
  data[4] = 0x03 # CMD id

  data[7] = 0x30 # register/address
  data[8] = 0x02 # length
  data[9] = 0x00 # value 
  data[10] = 0x00 # val

  data[5] = (data[2] ^ data[3] ^ data[4] ^ data[7] ^ data[8] ^ data[9]) & 0xFE
  #print("checksum1: ", hex(data[5]))
  data[6] = (~data[5]) & 0xFE
  #print("checksum2: ", hex(data[6]))

  i = 0
  while(i < 11):
    #print(data[i])
    ser.write(bytes([data[i]]))
    i += 1

def changeIDEEP(sid, newid):
  data = [0] * 10
  data[0] = 0xFF # header 1
  data[1] = 0xFF # header 2
  data[2] = 10 # length
  data[3] = sid # servo id
  data[4] = 0x01 # CMD id

  data[7] = 0x06 # register/address
  data[8] = 0x01 # length
  data[9] = newid # value 

  data[5] = (data[2] ^ data[3] ^ data[4] ^ data[7] ^ data[8] ^ data[9]) & 0xFE
  #print("checksum1: ", hex(data[5]))
  data[6] = (~data[5]) & 0xFE
  #print("checksum2: ", hex(data[6]))

  i = 0
  while(i < 10):
    #print(i, data[i])
    ser.write(bytes([data[i]]))
    i += 1

def changeMin(sid, minpos1, minpos2):
  data = [0] * 11
  data[0] = 0xFF # header 1
  data[1] = 0xFF # header 2
  data[2] = 11 # length
  data[3] = sid # servo id
  data[4] = 0x01 # CMD id

  data[7] = 20 # register/address
  data[8] = 0x02 # length
  data[9] = minpos1 # value 
  data[10] = minpos2

  data[5] = (data[2] ^ data[3] ^ data[4] ^ data[7] ^ data[8] ^ data[9] ^ data[10]) & 0xFE
  #print("checksum1: ", hex(data[5]))
  data[6] = (~data[5]) & 0xFE
  #print("checksum2: ", hex(data[6]))

  i = 0
  while(i < 11):
    #print(i, data[i])
    ser.write(bytes([data[i]]))
    i += 1

def changeMax(sid, maxpos1, maxpos2):
  data = [0] * 11
  data[0] = 0xFF # header 1
  data[1] = 0xFF # header 2
  data[2] = 11 # length
  data[3] = sid # servo id
  data[4] = 0x01 # CMD id

  data[7] = 22 # register/address
  data[8] = 0x02 # length
  data[9] = maxpos1 # value 
  data[10] = maxpos2

  data[5] = (data[2] ^ data[3] ^ data[4] ^ data[7] ^ data[8] ^ data[9] ^ data[10]) & 0xFE
  #print("checksum1: ", hex(data[5]))
  data[6] = (~data[5]) & 0xFE
  #print("checksum2: ", hex(data[6]))

  i = 0
  while(i < 11):
    #print(i, data[i])
    ser.write(bytes([data[i]]))
    i += 1

def statx(sid):
  data = [0] * 7
  data[0] = 0xFF # header 1
  data[1] = 0xFF # header 2
  data[2] = 0x07 # length
  data[3] = sid # servo id
  data[4] = 0x07 # CMD id

  data[5] = (data[2] ^ data[3] ^ data[4]) & 0xFE
  #print("checksum1: ", hex(data[5]))
  data[6] = (~data[5]) & 0xFE
  #print("checksum2: ", hex(data[6]))

  i = 0
  while(i < 7):
    #print(i, data[i])
    ser.write(bytes([data[i]]))
    i += 1

  while not(ser.inWaiting()):
    pass

  n = 0
  while(ser.inWaiting()):
    #print(bin(int(ser.read().hex(), base=16)))
    print(n, ser.read().hex())
    n += 1

def statxgetid(sid):
  data = [0] * 7
  data[0] = 0xFF # header 1
  data[1] = 0xFF # header 2
  data[2] = 0x07 # length
  data[3] = sid # servo id
  data[4] = 0x07 # CMD id

  data[5] = (data[2] ^ data[3] ^ data[4]) & 0xFE
  #print("checksum1: ", hex(data[5]))
  data[6] = (~data[5]) & 0xFE
  #print("checksum2: ", hex(data[6]))

  i = 0
  while(i < 7):
    #print(i, data[i])
    ser.write(bytes([data[i]]))
    i += 1

  while not(ser.inWaiting()):
    pass

  n = 0
  while(ser.inWaiting()):
    #print(bin(int(ser.read().hex(), base=16)))
    serread = ser.read()
    if (n == 3):
      returnId = int.from_bytes(serread, "big")
    #print(n, serread.hex())
    print(n, bin(int(serread.hex(), base=16)), "\t", serread.hex())
    n += 1
  
  return returnId

def changeIDEEPx(nid):
  changeIDEEP(statxgetid(0xFE), nid)


def moveServo(servoId, pos, color):
  lo_pos = np.uint8(pos)
  hi_pos = np.uint8((pos >> 8))

  data = [0] * 12
  data[0] = 0xFF # header 1
  data[1] = 0xFF # header 2
  data[2] = 12 # length
  data[3] = servoId # servo id
  data[4] = 0x06 # CMD id

  data[7] = 60 # playtime
  data[8] = lo_pos # jog lsb
  data[9] = hi_pos # jog msb
  color = color & 0x03
  data[10] = (color << 2) & (~0x02) # set
  data[11] = servoId # id

  data[5] = (data[2] ^ data[3] ^ data[4] ^ data[7] ^ data[8] ^ data[9] ^ data[10] ^ data[11]) & 0xFE # checksum1
  data[6] = (~data[5]) & 0xFE # checksum2

  i = 0
  while(i < 12):
    #print(data[i])
    ser.write(bytes([data[i]]))
    i += 1

def targetPosition(pos, color):
  moveServo(3, pos, color)
  moveServo(6, pos, color)
  #moveServo(0x01, pos, color)

def posTest(nid, color):
  torqueOn()
  #while(1):
  moveServo(nid, 0, 0x01)
  sleep(1)
  moveServo(nid, 512, 0x02)
  sleep(1)
  moveServo(nid, 1023, 0x01)
  sleep(1)
  moveServo(nid, 512, 0x02)
  sleep(1)

def rollback(sid):
  data = [0] * 9
  data[0] = 0xFF # header 1
  data[1] = 0xFF # header 2
  data[2] = 9 # length
  data[3] = sid # servo id
  data[4] = 0x08 # CMD id

  data[7] = 0x00 # id skip
  data[8] = 0x00 # band skip

  data[5] = (data[2] ^ data[3] ^ data[4] ^ data[7] ^ data[8]) & 0xFE
  #print("checksum1: ", hex(data[5]))
  data[6] = (~data[5]) & 0xFE
  #print("checksum2: ", hex(data[6]))

  i = 0
  while(i < 9):
    #print(data[i])
    ser.write(bytes([data[i]]))
    i += 1
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

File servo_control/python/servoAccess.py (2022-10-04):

import serial

# will later implement a code to find and connect to serial ports

ser = serial.Serial('/dev/ttyUSB2', 115200) # '/dev/ttyUSB0' on linux
#res = ser.read()
#print(res)


# packet to make LED green
header = 0xFF
packetSize = 0x0A # 10
pID = 0x02
cmd = 0x03

data0 = 0x35 # 53
data1 = 0x01
data2 = 0x01

checkSum1 = 0xC0 #(packetSize ^ pID ^ cmd ^ data0 ^ data1) and 0xFE
checkSum2 = 0x3E #(~checkSum1) and 0xFE

ser.write(header)
ser.write(packetSize)
ser.write(pID)
ser.write(cmd)
ser.write(checkSum1)
ser.write(checkSum2)
ser.write(data0)
ser.write(data1)
ser.write(data2)

ser.close()

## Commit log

2022-10-04 Add hexapod kinematics simulation
    Blender and Python scripting files
    [scripting.blend]
2022-10-04 Add hexapod model
    Blender files, acrylic blueprints, stl and gcode exports
    [_BASE.stl, _BASEx9899T.stl, _BODYx100.stl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]
2022-10-04 Add servo control code
    Servo manual, control through Arduino microcontroller, control with Python
